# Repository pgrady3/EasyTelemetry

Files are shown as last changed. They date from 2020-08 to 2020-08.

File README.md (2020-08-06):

# EasyTelemetry

A simple telemetry board designed to measure many useful things on an Eco-Marathon car. This board will log quantities to an SD card for later analysis, in addition to providing useful information to the driver on an LCD. This design is hopefully easy to extend.

## Features
* 15v-60v operation
* Based on Teensy 3.2 microcontroller
* Uses INA226 for measuring voltage and low-side current
* Measures vehicle speed using hall gear-tooth sensor
* Measures vehicle position using cheap Chinese Ublox NEO-6M GPS modules
* Integrates instataneous power into total energy (joules) consumed
* Compatible with cheap Chinese 20x4 displays with I2C "LCD backpack"
* Uses TE VAL-U-LOK connectors

## Output File

The software creates log files in the following format

```
39.542 2.804 110.87 5.53 294087.16 5380.27 1407101 4.6546335 114.4687347
39.511 3.111 122.93 5.51 294099.44 5380.78 1407201 4.6546288 114.4687347
39.437 3.854 151.98 5.49 294114.66 5381.30 1407301 4.6546235 114.4687347
39.437 3.854 151.98 5.48 294129.84 5381.82 1407401 4.6546183 114.4687347
39.092 7.068 276.28 5.48 294157.47 5382.34 1407501 4.6546135 114.4687347
39.020 7.721 301.29 5.49 294187.59 5382.85 1407601 4.6546082 114.4687347
```

corresponding to
```
voltage(V) current(A) power(w) velocity(m/s) energy(J) distance(m) elapsed time(ms) latitude(DD.dddd) longitude(DD.dddd)
```

## Schematic

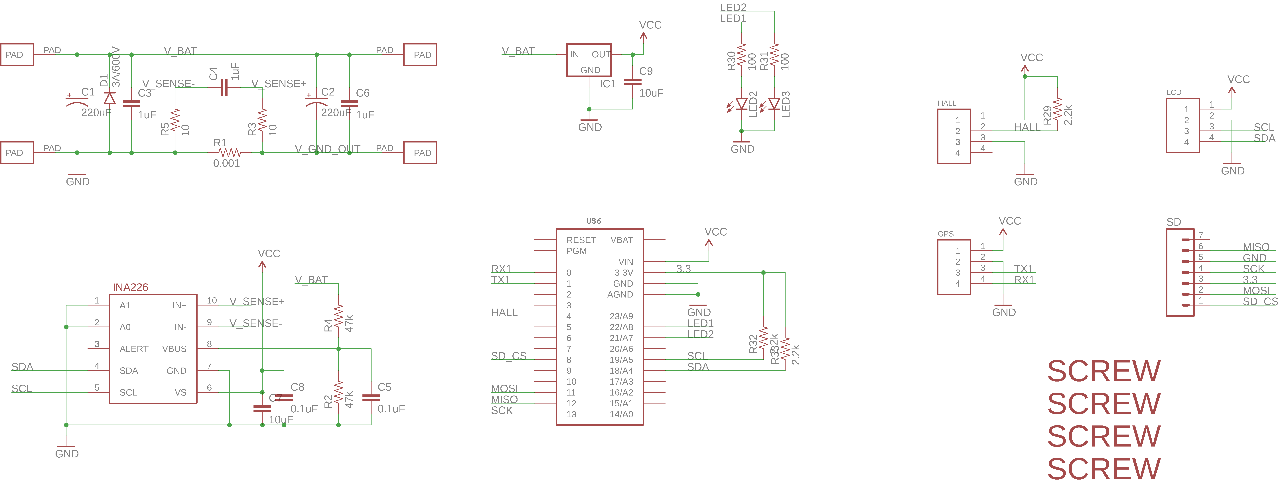
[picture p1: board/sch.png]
Schematic


## Board

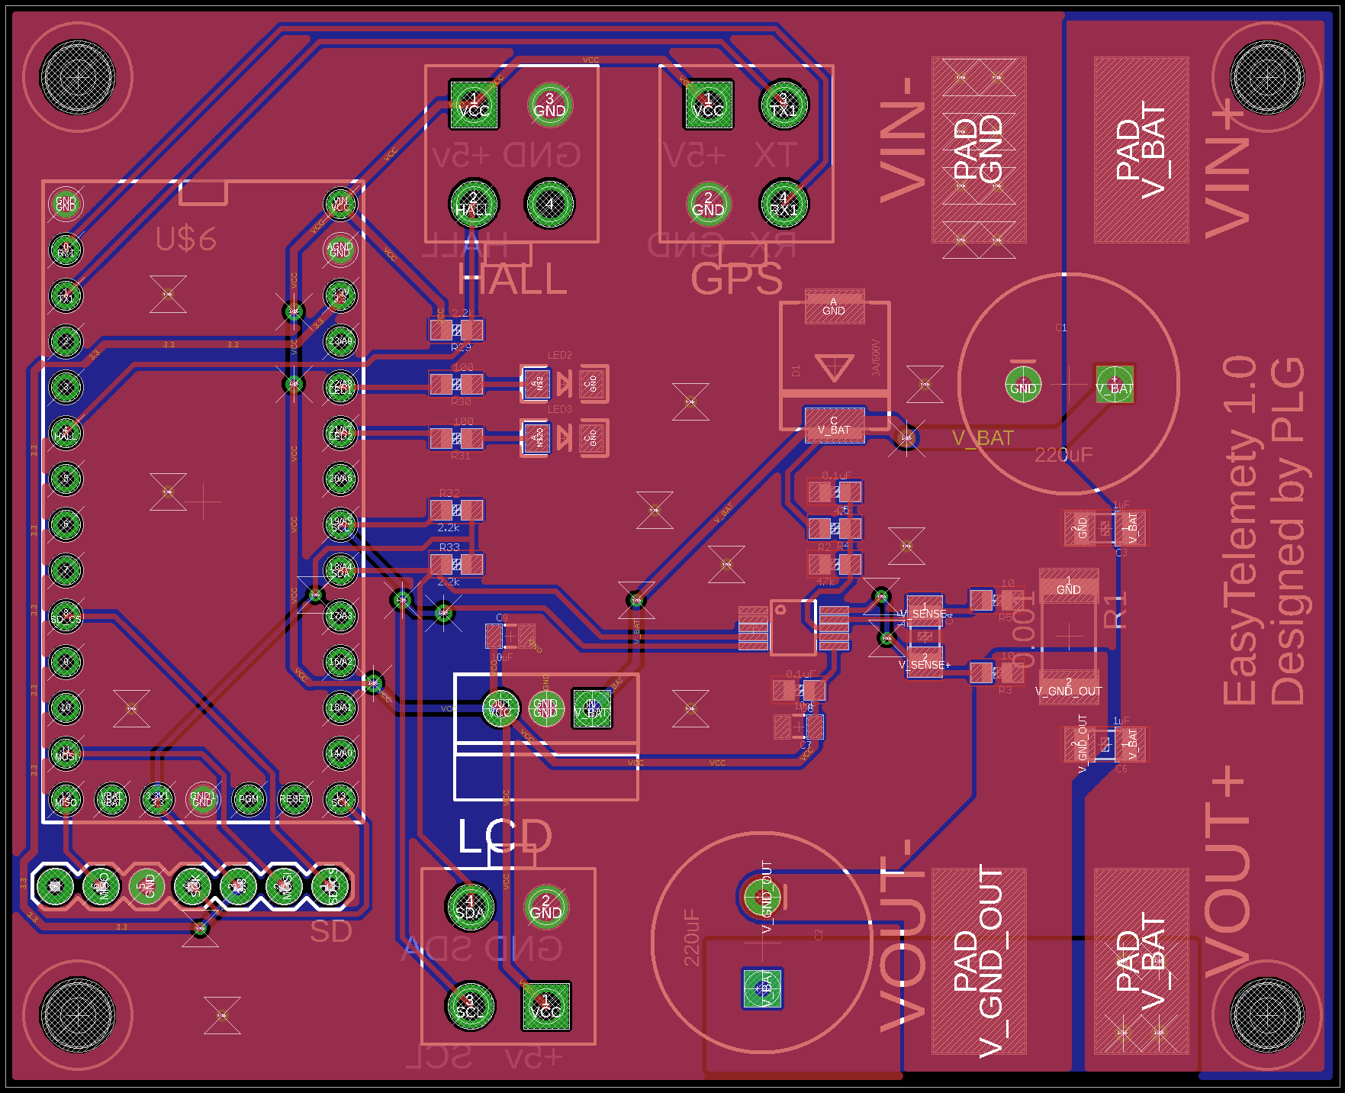
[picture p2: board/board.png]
Board


## Software Used

* PCB layout: [Eagle](https://www.autodesk.com/products/eagle/free-download)
* Compiler: [Arduino](https://www.arduino.cc/) with [PJRC Teensyduino add-on](https://www.pjrc.com/teensy/td_download.html)

## Assembly

This respository includes Gerber files which can be directly submitted to PCB manufacturers. We recommend Chinese manufacturers such as [AllPCB](https://www.allpcb.com/) or [JLCPCB](https://jlcpcb.com/). The repository also includes a Bill of Materials (BOM) with Digikey part numbers to order from.

Assembly is straightforward. However, it is recommended to cut the VIN-VUSB trace on the [underside of the Teensy](https://www.pjrc.com/teensy/card7b_rev1.pdf). Cutting the trace means that the Teensy can no longer be powered over USB. This is a safety procaution to prevent the controller feeding power backwards into your computer's USB port. 

## Contact Us

This controller was designed by Patrick Grady from Duke Electric Vehicles. If you need help or clarification, please [send us a message on our website.](http://www.duke-ev.org/dev-contact-us)

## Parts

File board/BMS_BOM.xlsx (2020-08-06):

Digikey part | Description | Value | Price | Qty | Subtotal | Total | 42.33
296-29034-1-ND | Power Measurement IC | INA226 | 2.88 | 1 | 2.88
1470-4531-ND | Switching reg | 5v | 8 | 1 | 8
696-1186-1-ND | Shunt resistor | 2mOhm | 0.71 | 1 | 0.71
493-1357-ND | Aluminum cap | 330uF | 0.6 | 2 | 1.2
1276-1068-1-ND | Ceramic cap | 1uF | 0.17 | 3 | 0.51
1276-2405-1-ND | Ceramic cap | 10uF | 0.14 | 2 | 0.28
160-1456-1-ND | LED | Green, 1206 | 0.34 | 2 | 0.68
732-9789-1-ND | TVS | 54V | 0.5 | 1 | 0.5
 |  |  |  |  | 0
1568-1231-ND | Teensy 3.2 |  | 22.5 | 1 | 22.5
1568-1345-ND | MicroSD breakout |  | 3.95 | 1 | 3.95
A30603-ND | Val-U-Lok | 4 pin | 0.56 | 2 | 1.12
 |  |  |  |  | 0
RMCF0603JT100RCT-ND | Resistor | 100 |  | 2
1276-1931-1-ND | Capacitor | 0.1uF |  | 2
RMCF0603JT10R0CT-ND | Resistor | 10 |  | 2
RMCF0603JT2K20CT-ND | Resistor | 2.2k |  | 3
P20162CT-ND | Resistor | 47k |  | 2 | 0
 |  |  |  |  | 0
NEO-6M GPS | GPS module |  |  | 1 | 0
https://www.ebay.com/itm/Yellow-Serial-IIC-I2C-TWI-2004-204-20X4-Character-LCD-Module-Display-For-Arduino/201478544229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 | LCD I2C |  |  | 1
CE3006N-41-25-ND | Wire
55505-00-02-A-ND | Hall, honeywell style
CH398-ND | Hall, screw style

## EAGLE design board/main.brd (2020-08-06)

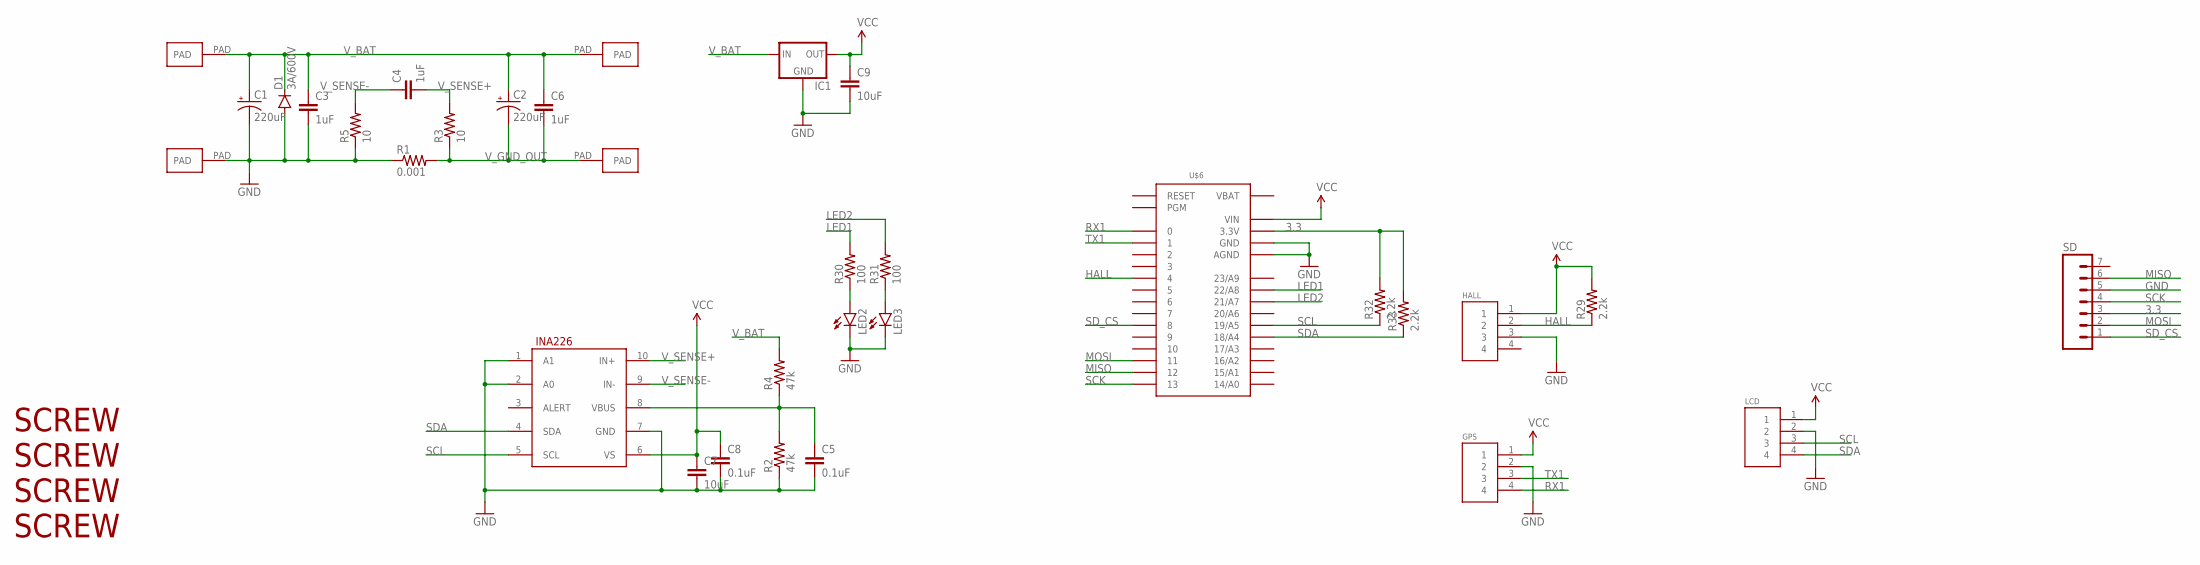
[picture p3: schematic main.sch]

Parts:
C1, C2: 220uF; CPOL-RADIAL-1000UF-25V
C3, C4, C6: 1uF; 1206
C5, C8: 0.1uF; 0603-CAP
C7, C9: 10uF; 0805
D1: 3A/600V; SMC
GPS: GPS; 4PINVALULOK
HALL: HEADER4VALULOK; 4PINVALULOK
IC1: V_REG_78XXSINK; TO220-IGO
LCD: GPS; 4PINVALULOK
LED2, LED3: LED1206; LED-1206
R1: 0.001; R2512
R2, R4: 47k; 0603-RES
R3, R5: 10; 0603-RES
R29, R32, R33: 2.2k; 0603-RES
R30, R31: 100; 0603-RES
SD: M07; 1X07
U$1: INA226; PSOP-10
U$2, U$3, U$4, U$5: PAD
U$6: TEENSY_3.0_BASIC
U$13, U$14, U$15, U$16: SCREW; M3HOLE

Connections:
3.3: R32.2, R33.2, SD.3, U$6.3.3V, U$6.3.3V1 (3.3V)
GND: C1.-, C3.2, C5.2, C7.2, C8.2, C9.2, D1.A, GPS.2, HALL.3, IC1.GND, LCD.2, LED2.C, LED3.C, R1.1, R2.1, R5.1, SD.5, U$1.1 (A1), U$1.2 (A0), U$1.7 (GND), U$3.PAD, U$6.AGND, U$6.GND, U$6.GND1 (GND)
HALL: HALL.2, R29.1, U$6.4
LED1: R30.2, U$6.22/A8
LED2: R31.2, U$6.21/A7
MISO: SD.6, U$6.12
MOSI: SD.2, U$6.11
unnamed: C5.1, R2.2, R4.1, U$1.8 (VBUS)
unnamed: LED2.A, R30.1
unnamed: LED3.A, R31.1
RX1: GPS.4, U$6.0
SCK: SD.4, U$6.13
SCL: LCD.3, R32.1, U$1.5 (SCL), U$6.19/A5
SDA: LCD.4, R33.1, U$1.4 (SDA), U$6.18/A4
SD_CS: SD.1, U$6.8
TX1: GPS.3, U$6.1
VBAT: U$6.VBAT
VCC: C7.1, C8.1, C9.1, GPS.1, HALL.1, IC1.OUT, LCD.1, R29.2, U$1.6 (VS), U$6.VIN
V_BAT: C1.+, C2.+, C3.1, C6.1, D1.C, IC1.IN, R4.2, U$2.PAD, U$4.PAD
V_GND_OUT: C2.-, C6.2, R1.2, R3.1, U$5.PAD
V_SENSE+: C4.2, R3.2, U$1.10 (IN+)
V_SENSE-: C4.1, R5.2, U$1.9 (IN-)

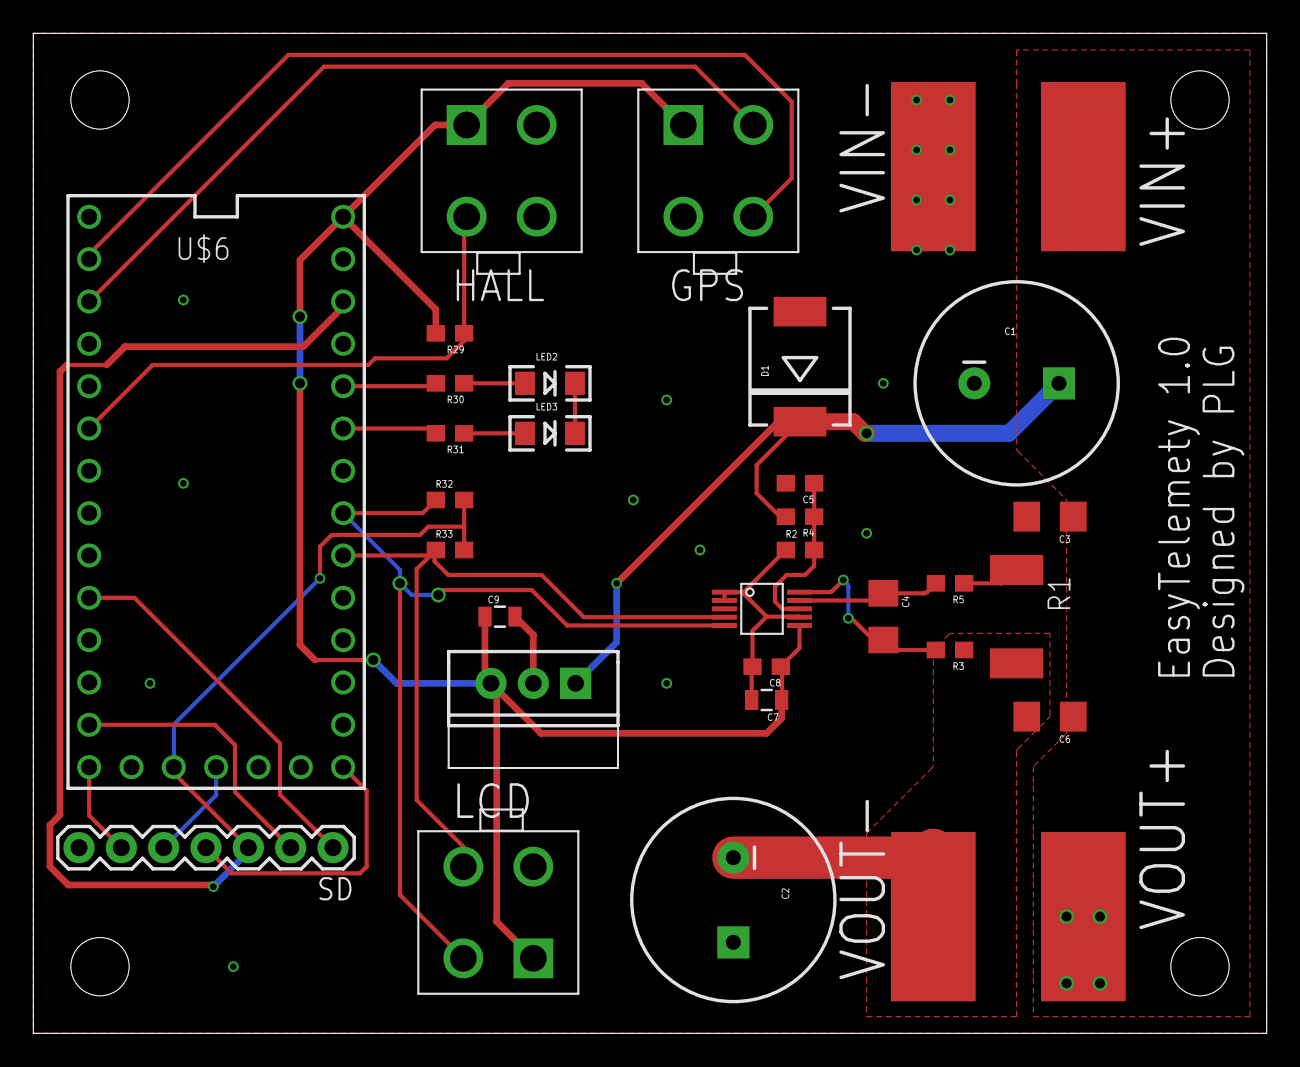
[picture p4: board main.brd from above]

Board: 2 copper layers, 74.0 x 60.0 mm, 37 parts (0 on the bottom side), 21 nets.

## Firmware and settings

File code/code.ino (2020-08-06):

#include <i2c_t3.h>
#include <SD.h>
#include "Adafruit_GPS.h"
#include "LiquidCrystal_I2C.h"
#include "INA.h"

#define LED1 21
#define LED2 22

#define HALL 4
#define SD_CS 8

#define WHEEL_CIRC 1.552
#define WHEEL_TICKS 9
#define TICK_DIST (WHEEL_CIRC / WHEEL_TICKS)

#define TARGET_CURRENT 5

volatile uint32_t tickTimes[WHEEL_TICKS];
volatile uint32_t tickPos;

volatile uint32_t loopTime = 0;
volatile uint32_t lastHallPulse = 0;
volatile uint32_t lastInaMeasurement = 0;
volatile uint32_t countIntervals = 0;
volatile int32_t avgdT = 1000000;
volatile uint32_t distTicks = 0;

double energyUsed = 0.0;
double distance = 0.0;
double currentSpeed = 0.0;
double currentRPM = 0.0;
double InaVoltage = 0.0;
double InaCurrent = 0.0;
double InaPower = 0;
double batteryVoltage = 0.0;
double effScore = 0;

File myFile;
Adafruit_GPS GPS(&Serial1);
LiquidCrystal_I2C lcd(0x27, 20, 4);

void setup() {
  Wire.begin(I2C_MASTER, 0x00, I2C_PINS_18_19, I2C_PULLUP_EXT, 400000);
  INAinit();

  Serial.begin(115200);
  SD.begin(SD_CS);
  lcd.begin();
  lcd.backlight();
  lcd.print("Hello, world!");

  pinMode(LED1, OUTPUT);
  pinMode(LED2, OUTPUT);
  digitalWrite(LED1, HIGH);
  digitalWrite(LED2, HIGH);

  pinMode(HALL, INPUT_PULLUP);
  attachInterrupt(HALL, countHallPulse, FALLING);

  myFile = SD.open("data.txt", FILE_WRITE);
  
  GPSInit();
}

void loop() {  
  GPSPoll();//must be called rapidly
  
  uint32_t curTime = millis();
  if(curTime < loopTime + 100)//if less than 100ms, start over
    return;

  digitalWrite(LED2, !digitalRead(LED2));
  loopTime = curTime;
  
  updateINA();
  updateSpeed();

  writeToBtSd();
  /*char b = GPS.read();
  if(b)
    Serial.print(b);*/
}

void updateINA()
{
  InaVoltage = INAvoltage();
  InaCurrent = INAcurrent();
  InaPower = InaVoltage * InaCurrent;
  
  double currentInaTime = millis();
  energyUsed += InaPower * (currentInaTime - lastInaMeasurement) / 1000;
  lastInaMeasurement = currentInaTime;

  effScore = distance / energyUsed * 3600;
}

void updateSpeed()
{
  currentSpeed = 1000000.0 / avgdT * WHEEL_CIRC; 
  if(micros() - lastHallPulse > 2000000)//if nothing for more than 2 seconds, set speed to zero
    currentSpeed = 0;
  
  distance = distTicks * TICK_DIST;
}

void countHallPulse() {
  uint32_t current = micros();

  uint32_t prevTime = tickTimes[tickPos];// time 1 rev ago. fixed 7/5/2018 :(

  tickTimes[tickPos++] = current;
  tickPos %= WHEEL_TICKS;

  avgdT = current - prevTime;

  distTicks++;
  
  lastHallPulse = current;

  digitalWrite(LED1, (distTicks) & 1);
}

const unsigned char UBLOX_INIT[] = {
  0xB5, 0x62, 0x06, 0x08, 0x06, 0x00, 0x64, 0x00, 0x01, 0x00, 0x01, 0x00, 0x7A, 0x12,//(10Hz)
  0xB5, 0x62, 0x06, 0x01, 0x08, 0x00, 0xF0, 0x01, 0x00, 0x00, 0x00, 0x00, 0x00, 0x01, 0x01, 0x2B, // GxGLL off
  0xB5, 0x62, 0x06, 0x01, 0x08, 0x00, 0xF0, 0x03, 0x00, 0x00, 0x00, 0x00, 0x00, 0x01, 0x03, 0x39, // GxGSV off
  0xB5, 0x62, 0x06, 0x01, 0x08, 0x00, 0xF0, 0x05, 0x00, 0x00, 0x00, 0x00, 0x00, 0x01, 0x05, 0x47, // GxVTG off
  0xB5,0x62,0x06,0x01,0x08,0x00,0xF0,0x00,0x00,0x00,0x00,0x00,0x00,0x01,0x00,0x24, // GxGGA off
  0xB5,0x62,0x06,0x01,0x08,0x00,0xF0,0x02,0x00,0x00,0x00,0x00,0x00,0x01,0x02,0x32, // GxGSA off
  //0xb5, 0x62, 0x06, 0x00, 0x14, 0x00, 0x01, 0x00, 0x00, 0x00, 0xd0, 0x08, 0x00, 0x00, 0x00, 0xc2, 0x01, 0x00, 0x07, 0x00, 0x07, 0x00, 0x00, 0x00, 0x00, 0x00, 0xc4, 0x96, 0xb5, 0x62, 0x06, 0x00, 0x01, //baud rate 115200
  0xB5,0x62,0x06,0x00,0x14,0x00,0x01,0x00,0x00,0x00,0xD0,0x08,0x00,0x00,0x00,0xE1,0x00,0x00,0x07,0x00,0x03,0x00,0x00,0x00,0x00,0x00,0xDE,0xC9,//baud rate 57600
};

void GPSInit()
{
  GPS.begin(9600);
  for (uint32_t i = 0; i < sizeof(UBLOX_INIT); i++) {
    Serial1.write(UBLOX_INIT[i]);
  }
  
  delay(50);
  Serial1.end();
  
  delay(50);
  GPS.begin(57600);
}

void GPSPoll()
{
  while(GPS.read());
  
  if (GPS.newNMEAreceived())
    GPS.parse(GPS.lastNMEA());
}

void writeToBtSd() {
  String outputStr = String(InaVoltage, 3) + " " + String(InaCurrent, 3) + " " + String(InaPower) + " "+ String(currentSpeed) + " " +
                     String(energyUsed) + " " + String(distance) + " " + String(millis()) + " " + String(GPS.latitudeDegrees, 7) + 
                     " " + String(GPS.longitudeDegrees, 7);
  
  Serial.println(outputStr);//usb 
  //Serial.println(GPS.milliseconds); 
  GPSPoll();//super hacky bc short GPS buffer
  
  myFile.println(outputStr);
  myFile.flush();//need this to make sure we actually write to card and don't buffer

  GPSPoll();//super hacky bc short GPS buffer

  lcd.clear();
  LCDWriteFloat(0, 0, InaVoltage, " V");
  LCDWriteFloat(0, 1, InaCurrent, " A");  
  LCDWriteInt(0, 3, GPS.milliseconds, " ms");

  LCDWriteFloat(10, 0, currentSpeed * 3.6, " km/h");
  LCDWriteFloat(10, 1, InaPower, " W");
  LCDWriteFloat(8, 3, effScore, " km/kWh");
}


void LCDWriteFloat(uint8_t x, uint8_t y, float data, const char* s2)
{
  lcd.setCursor(x, y);
  lcd.print(data);
  lcd.print(s2);
  GPSPoll();
}

void LCDWriteInt(uint8_t x, uint8_t y, uint32_t data, const char* s2)
{
  lcd.setCursor(x, y);
  lcd.print(data);
  lcd.print(s2);
  GPSPoll();
}

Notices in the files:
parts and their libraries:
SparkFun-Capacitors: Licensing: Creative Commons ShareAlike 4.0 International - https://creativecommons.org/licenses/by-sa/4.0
